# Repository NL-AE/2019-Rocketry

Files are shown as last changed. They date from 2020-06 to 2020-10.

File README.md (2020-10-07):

# 2019 Rocketry

Rocket for entry into the 2019 UKRoC challenge with 5 other friends.

Launch day: we put 4 motors instead of 3 and the rocket flew some 380m (about 120m over target). We lost the bottom stage so we now have half a rocket. 

In retrospective, painting it camouflage green was also not a good idea considering it landed in a green field.
Also I made the arduino write to the "DATALOG.TXT" instead of the file in the SD card called "data.txt" so we didnt get any data.

The control system looked like it worked since the rocket didnt have a rapid unplanned disassembly and shot straight upwards.

Before Launch
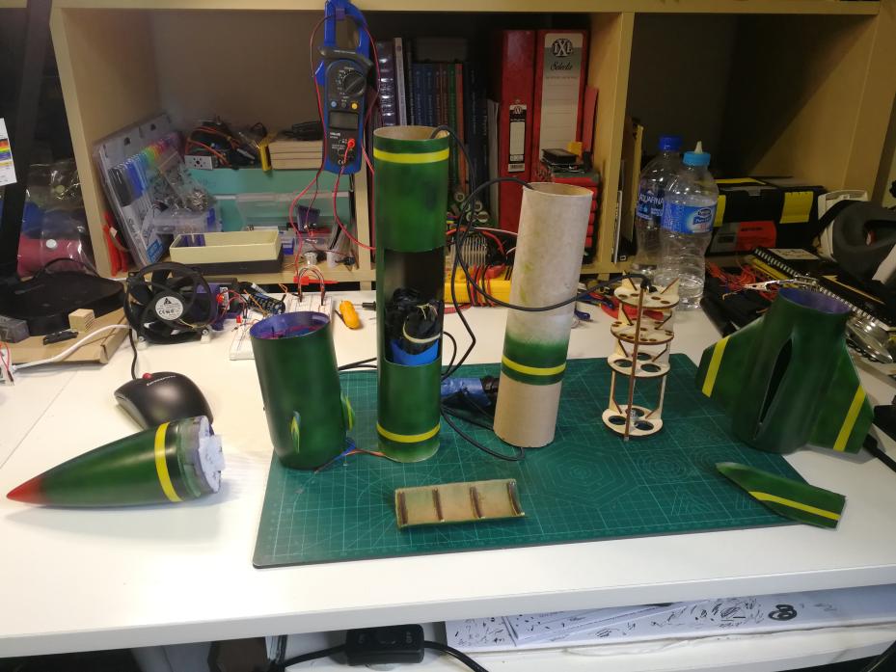
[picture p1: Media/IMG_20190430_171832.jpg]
Rocket in pieces


Ready for launch
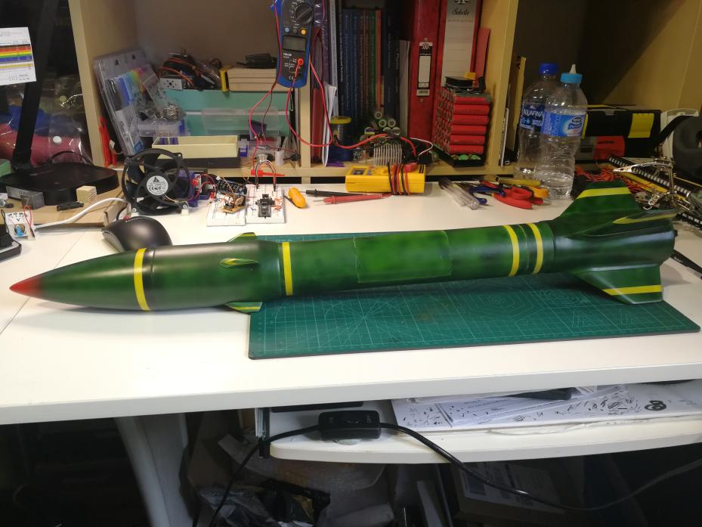
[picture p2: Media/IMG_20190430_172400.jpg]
Rocket togeter


The pile of electronics that controls it
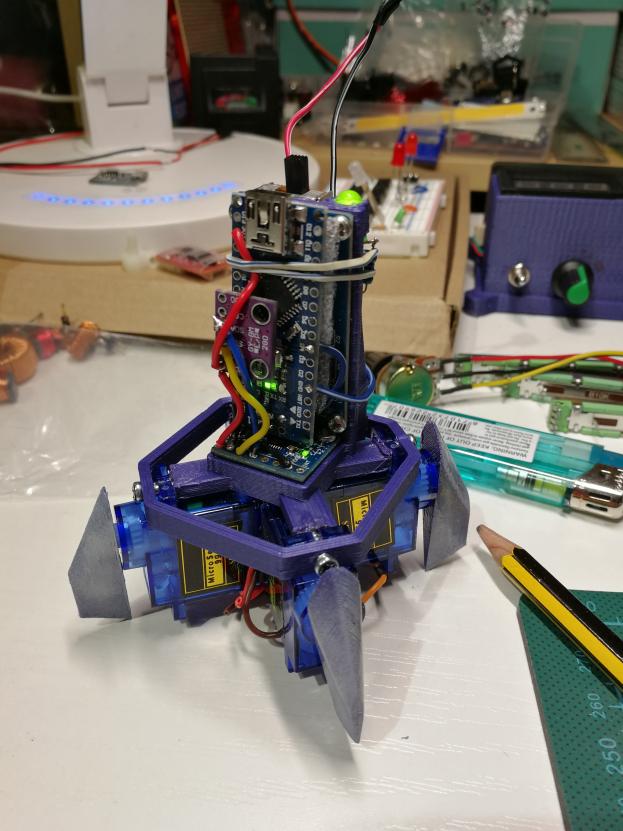
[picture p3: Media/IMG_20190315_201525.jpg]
Arduino pile


The launchpad that plugs into a camera tripod
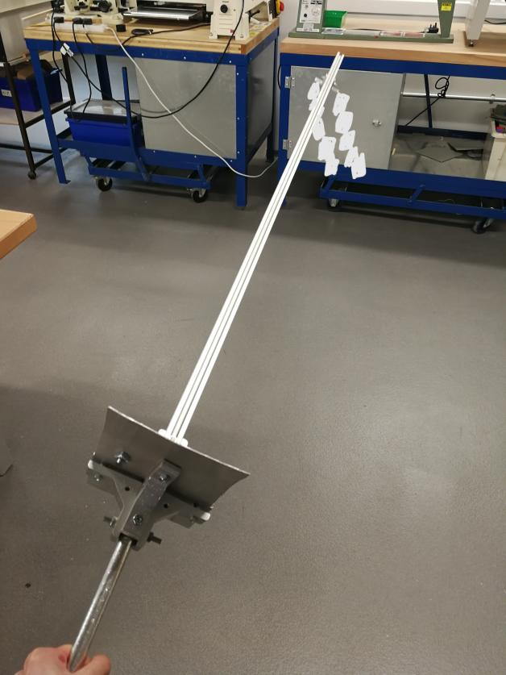
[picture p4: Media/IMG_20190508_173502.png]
Launchpad


Big red launch button that we didnt end up using
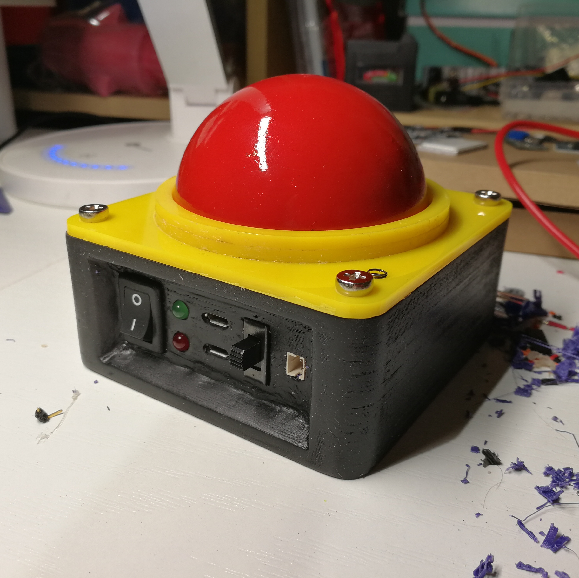
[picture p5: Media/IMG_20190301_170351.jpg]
button


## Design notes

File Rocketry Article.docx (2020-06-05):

Is it possible to create a self-stabilizing rocket?

Well yes of course, nowadays almost all missiles have a guidance system that allows for trajectories to be calculated and finely controlled. Despite the widespread use of this technology, it is mainly restricted to large corporations with huge RnD departments however, the rise of consumer electronics recently had given the ability for individuals to create complex circuitry and controllers. This will be the focus of this endeavour, is it possible to create a self-stabilizing model scale rocket?

The Control System

The brainbox of this operation will be the Arduino, a small programmable micro-controller (essentially a very small computer) which will read the pitch, yaw and roll as well as the altitude of the rocket and use that to control the angle of four fins mounted to the top of the rocket.

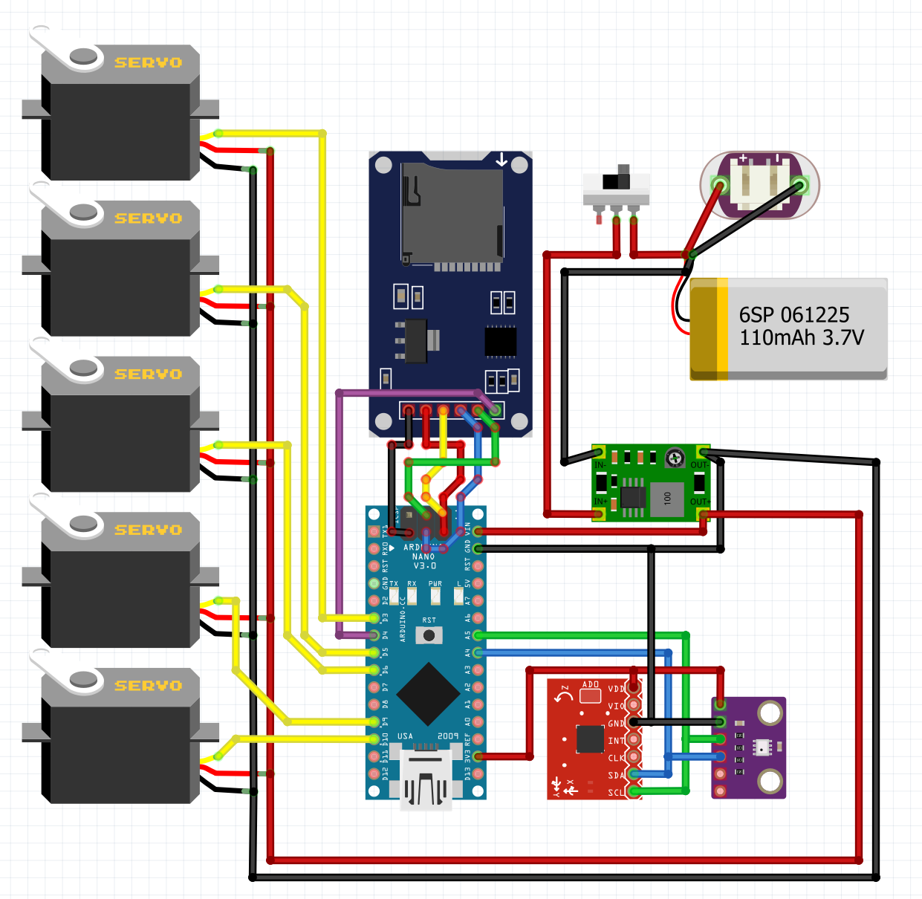
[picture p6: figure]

Secondary aims include to calculate the altitude of the rocket from atmospheric pressure readouts and to hopefully extrapolate velocity from it. Another aim is to use a SD card to record the data from the rocket and be able to act as a datalogger for analysis after launches.

Boost converter

Li-po battery

Power switch

Charging port

Gyroscope

Altimeter

SD card reader

Arduino

Circuit Diagram

Data input and outputs

Firstly, powering the components:

1) The voltage from the lithium polymer (li-po) battery is boosted from 3.7v (nominal cell voltage) to 6.0v since the other electronics run on 5v logic. The additional 1v is needed since there will be a small 0.7v voltage drop from the power regulator on the Arduino.
2) The Arduino then powers the gyroscope and altimeter at 3.3v since they run on 3.3v logic and will most likely become damaged when powered at 5v.
3) The servos are connected directly to the boost converter’s 6v as it means that no current needs to run through the Arduino to get to the servos. This is important as the servos will be drawing about 100mA under no load, and up to 500mA at full which the Arduino cannot supply without burning up.

Secondly, the controls:

1) The Arduino communicates with the modules and reads the angles off the gyroscope and the pressure off the altimeter, receiving data in the format of:

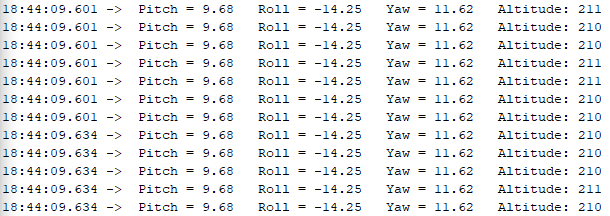
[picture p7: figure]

2) Since the altimeter outputs pressure in pascals, it needs to be converted into a altitude above sea level in Altitude(m)=13504.985×(1-((Pressure_(Pa))/101325)^0.190289 )

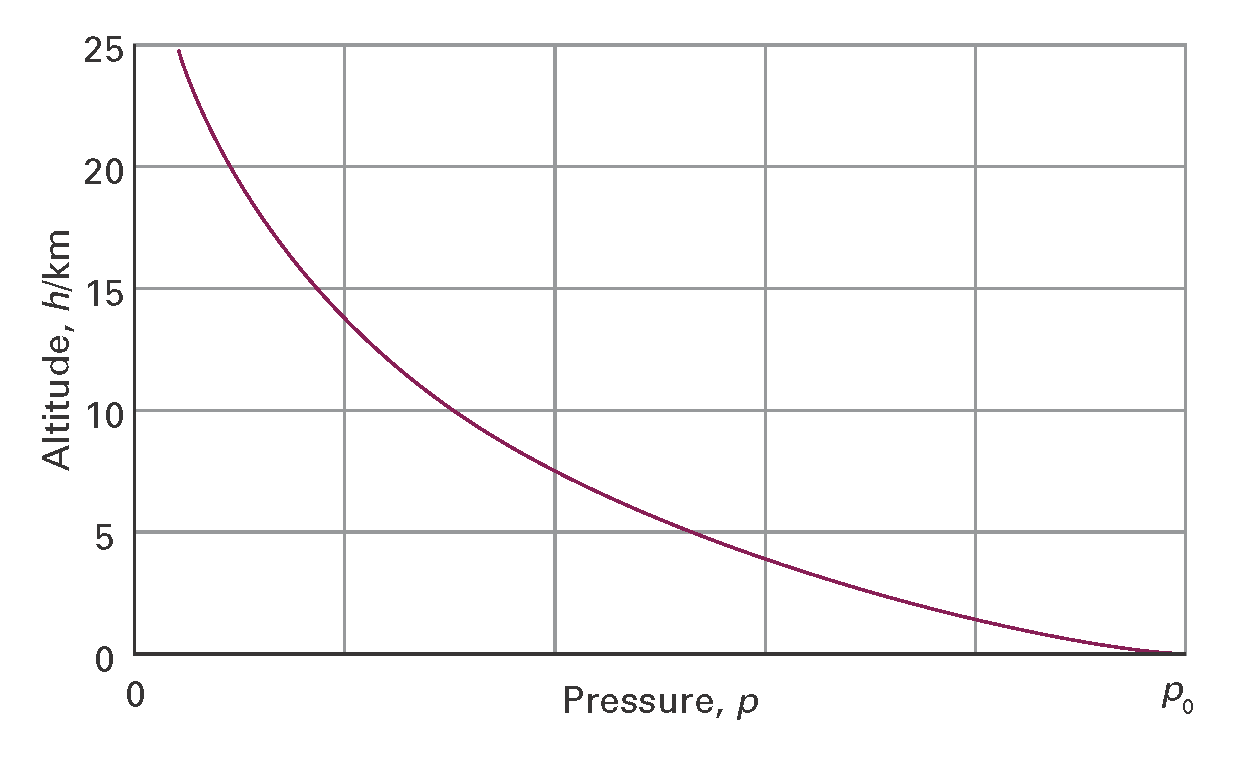
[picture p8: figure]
Image result for pressure to altitude formula

3) From the angles received, the Arduino will then send a signal to the servos along the yellow wires, instructing them to move to a different angle if necessary.

At this point, emerges the main problem of control, how much should the servos change angle?

PID controllers

If the angle change is too much, it will cause the rocket to over-correct, leading to the servos swinging back to correct the over-correction. This leads to a system that rapidly loses stability essentially balancing on a knife’s edge. What is needed is a system that actively measures the change in angle and corrects for it. Systems like this are called PID controllers and are used in inherently unstable scenarios such as self-balancing robots, temperature regulators or in this case, a model rocket.

PID controllers work by taking the difference in desired angle and current angle(called the “error”) and computing a needed angle change (called the “solution”) which is sent the servos to achieve that while monitoring the error constantly.

The 3 components of a PID controller are:

1) Proportional –

The controller takes the error and sets the solution to be proportional to that difference. If this is set too high, it will cause the problem as mentioned above and cause rapidly growing oscillations but set too low there will be little change in the error. Thus, something is needed to dampen the oscillations.

2) Derivative –

This considers the magnitude of the solution computed by the proportional and decreases it according to how small the error is. It is effectively a damper to the proportional part of the controller and stops the oscillations by lowering the solution according to how small the error it. However, another problem arises, if this is set too high, it will dampen the solution too much that the error will never be 0 (the system will never reach its desired value) as the dampening effect will become greater than the solution, leading to an equilibrium achieved just below the desired value. Thus, the last part of the PID controller is needed.

3) Integral –

This finds the integral between the current angle and the desired angle. The smaller the error, the larger this component becomes. It essentially pushes the solution just enough that the solution will become zero when the error is zero, thus achieving the desired angle.

Component | Too high | Too low
Proportional | Rapid oscillations | Changes very slowly
Derivative | Equilibrium achieved below desired angle | Rapid oscillations
Integral | Small, rapid oscillations | Never reaches desired angle

The main problem with controllers like this is that it requires extensive testing and tuning the constants for each of the components. Additionally, they constants would most likely need to change according to the relative wind speed, creating further problems.

Coupled with the need for complex calculations on the Arduino’s part just to compute the solution, as well as the resulting decreased refresh rate of this systems means that it is not very suitable for small scale rockets. It is possible to get around this hardware problem by using better micro-controllers however the prices for a control board rises very rapidly.

The Alternate Solution

The method of stabilization used in the end is a relatively simple system which has many advantages over a PID system. The process is:

1) Determining the angles of pitch, yaw and roll of the rocket.
2) Moving the servo motors so that they always are perpendicular to the ground, resulting in almost no further calculation needed as well as negating the opportunity for over-correcting to occur.

Working in 2 dimensions, if the rocket is angled slightly to the left, the fins pitch to the right (relative to the rocket) but remain perpendicular to the ground. This results in the rocket experiencing a force which pushes it to zero degrees or vertical.

In the end, we opted for this solution since it make the code a lot easier as well as being less demanding on the Arduino. This also meant that we did not need to perform any wind tunnel experiments to adjust the controller, also a highly time-consuming task. As stated above, the settings would most likely need to change according to wind speed and with the rocket reaching up to 70ms⁻¹, it would be impossible to simulate this in the wind tunnel setup we had.

Results

Following the launch on the 4th May, we saw that the correction system functioned perfectly with the rocket flying straight up, overshooting the desired height as it was our first launch. Unfortunately, due to the rocket reaching a high altitude of 371m, the rocket drifted on the parachutes for a very long distance away from the launch site, resulting in the bottom part of the rocket being lost, preventing us from performing further launches. Despite top half of the rocket containing the electronics being recovered, we collected no data due to either a programming error or other hardware errors.

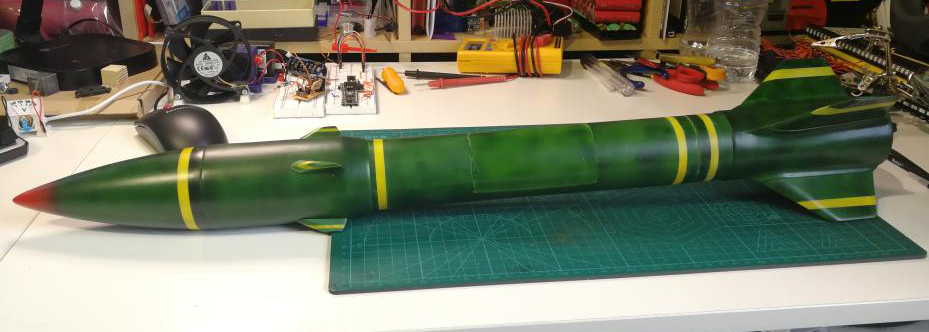
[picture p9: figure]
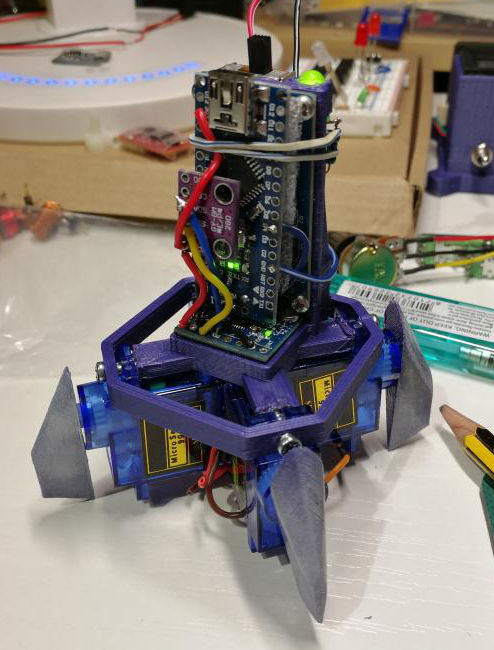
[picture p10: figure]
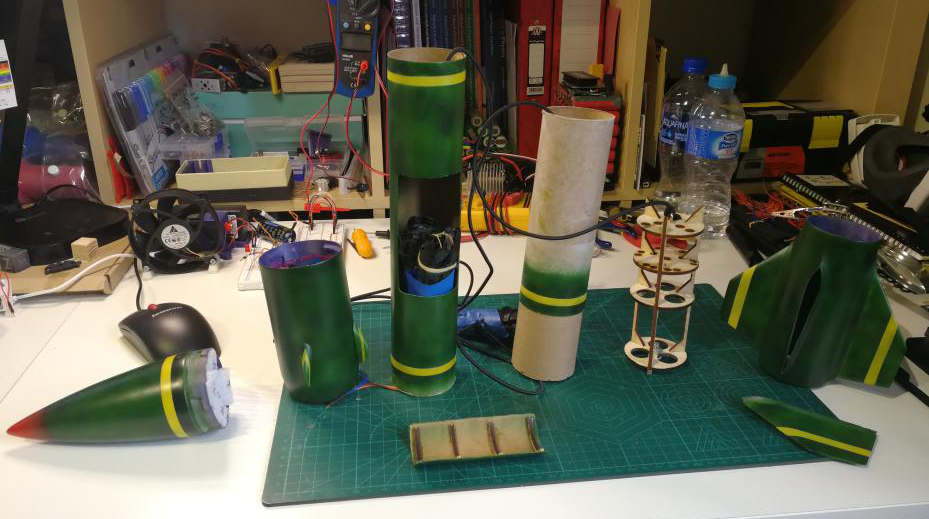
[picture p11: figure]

Left to right:

Nosecone, electronics bay, middle tube section, bottom stage, motor mounts, fin support structure.

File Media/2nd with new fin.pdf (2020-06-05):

## Rocket Design

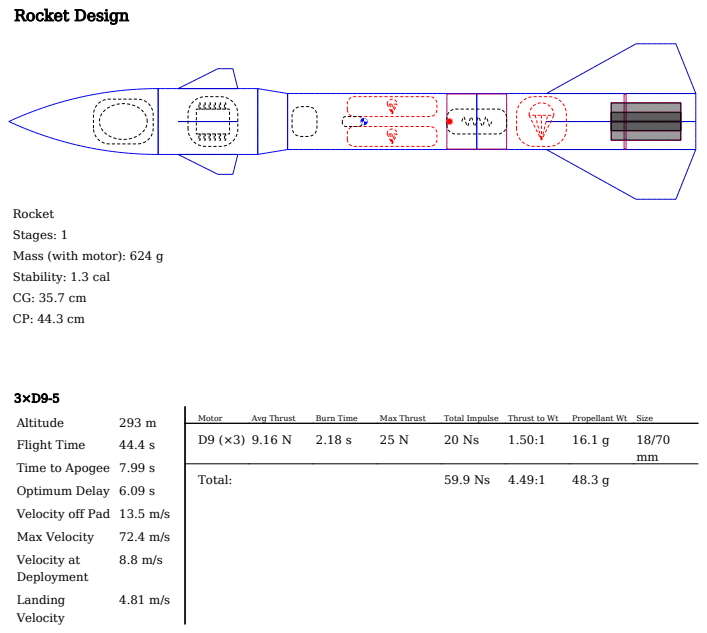
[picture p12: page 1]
Altitude; Flight Time; Optimum Delay 6.09 s; Max Velocity; Velocity at; Deployment; Landing; Velocity; Motor; Avg Thrust; Burn Time; Max Thrust; Total Impulse; Thrust to Wt; Propellant Wt Size; Total:

Rocket
Stages: 1
Mass (with motor): 624 g
Stability: 1.3 cal

Time to Apogee 7.99 s

Velocity off Pad 13.5 m/s

## Parts Detail

Sustainer

Nose cone | 3D Print

(1.23 g/cm³)

Ogive | Len: 15 cm | Mass: 20.7 g
Body tube | 3D Print

(1.23 g/cm³)

Diain 6.46 cm
Diaout 6.62 cm
Len: 10 cm | Mass: 20.2 g
Egg | Diaout 4.5 cm | Mass: 63 g
Arduino Fins (4) | 3D Print

(1.23 g/cm³)

Thick: 0.5 cm | Mass: 3 g
Arduino + Payloads | Diaout 5 cm | Mass: 73 g
Transition | 3D Print

(1.23 g/cm³)

Fore Dia: 6.62
cm
Aft Dia: 5.63
cm
Len: 3 cm | Mass: 8.46 g
Main Body | Cardboard

(0.68 g/cm³)

Diain 5.53 cm
Diaout 5.63 cm
| Len: 19 cm | Mass: 11.3 g
Parachute 1 | Ripstop nylon

(67 g/m²)

Diaout 50 cm | Len: 9 cm | Mass: 16.4 g
Shroud Lines | Elastic cord
(round 2 mm,
1/16 in)

(1.8 g/m)

Lines: 6 | Len: 30 cm
Parachute 1 | Ripstop nylon

(67 g/m²)

Diaout 50 cm | Len: 9 cm | Mass: 16.4 g
Shroud Lines | Elastic cord
(round 2 mm,
1/16 in)

(1.8 g/m)

Lines: 6 | Len: 30 cm
Parachute Servo | Diaout 1 cm | Mass: 10 g
Unspecified | Diaout 3 cm | Mass: 200 g
Boost | Cardboard

(0.68 g/cm³)

Diain | 5.54 cm
| Diaout 5.63 cm
Len: 22 cm | Mass: 11.8 g
Back Fins (4) | Balsa

(0.17 g/cm³)

| Thick: 1 cm | Mass: 27.5 g
Engines | Cardboard

(0.68 g/cm³)

Diain | 1.8 cm
| Diaout 1.9 cm
Len: 7 cm | Mass: 4.15 g
Tube Coupler | Cardboard

(0.68 g/cm³)

Diain | 5.34 cm
| Diaout 5.54 cm
Len: 6 cm | Mass: 6.97 g
Shock cord | Elastic cord
(round 2 mm,
1/16 in)

(1.8 g/m)

Len: 40 cm | Mass: 0.72 g
Parachute Back | Ripstop nylon

(67 g/m²)

Diaout 45 cm | Len: 5 cm | Mass: 13.9 g
Shroud Lines | Elastic cord
(round 2 mm,
1/16 in)

(1.8 g/m)

Lines: 6 | Len: 30 cm
Bulkhead | Cardboard

(0.68 g/cm³)

Diaout 5.54 cm Len: 0.2 cm Mass: 27 g

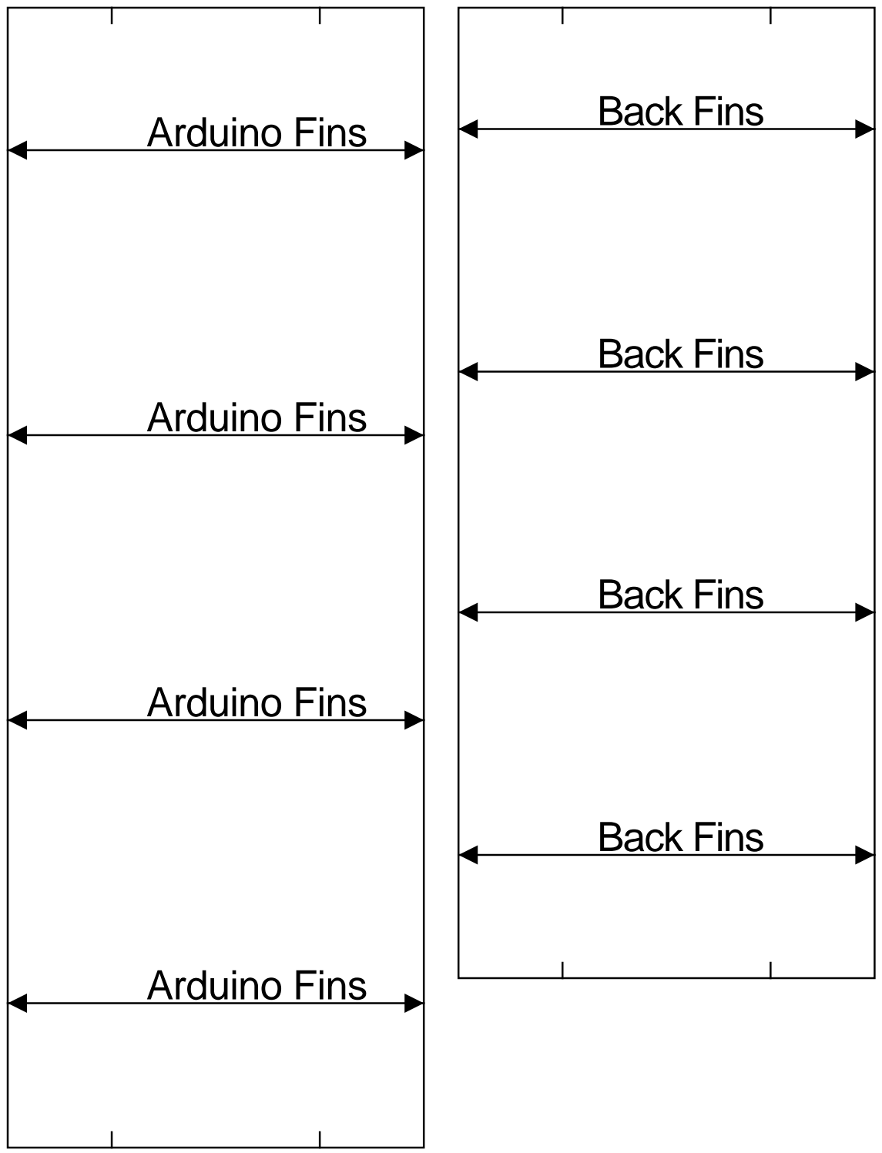
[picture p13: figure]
Arduino Fins; Back Fins

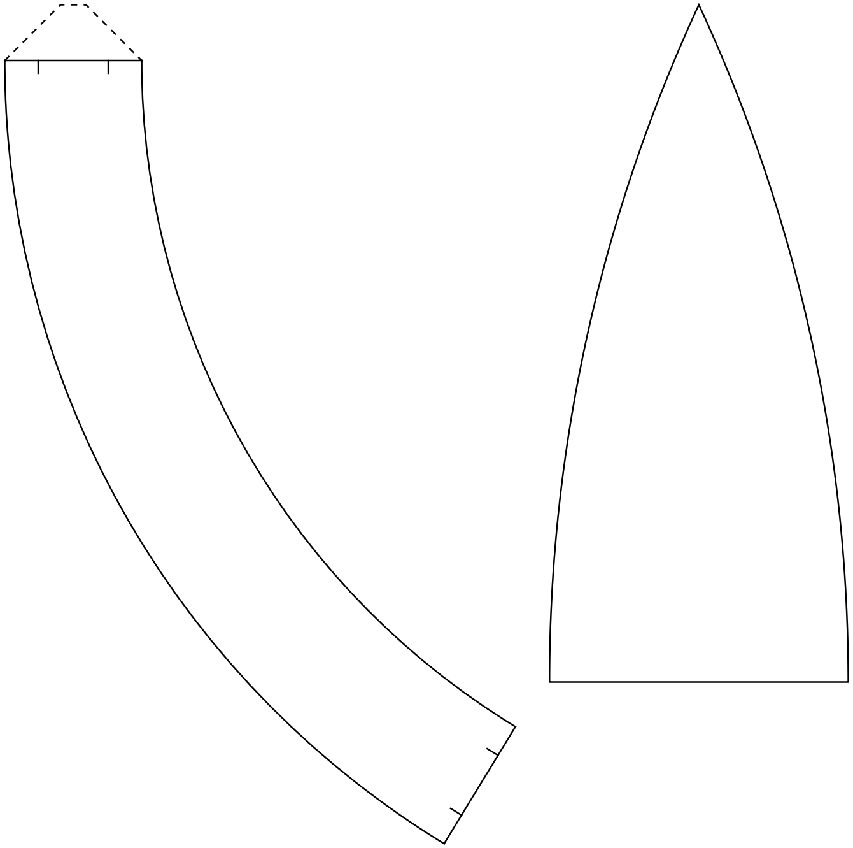
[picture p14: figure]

# in cm

cm
in

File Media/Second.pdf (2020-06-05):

## Rocket Design

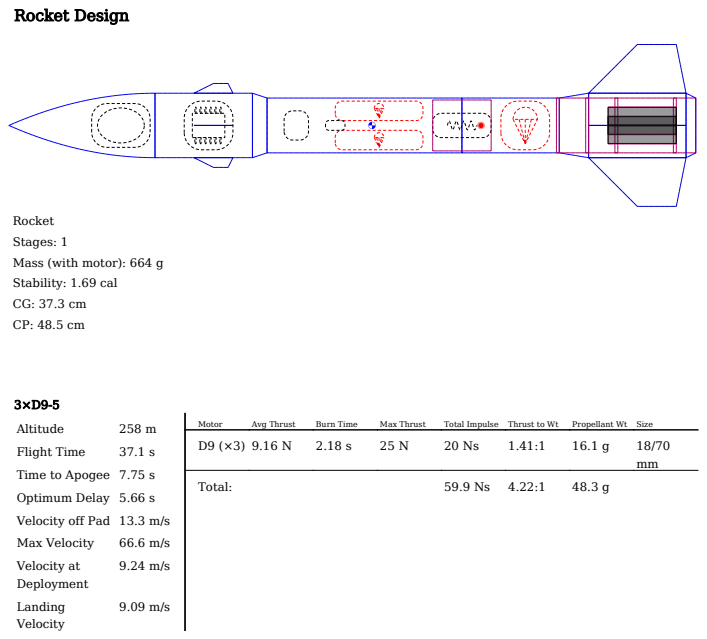
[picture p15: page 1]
Altitude; Flight Time; Optimum Delay 5.66 s; Max Velocity; Velocity at; Deployment; Landing; Velocity; Motor; Avg Thrust; Burn Time; Max Thrust; Total Impulse; Thrust to Wt; Propellant Wt Size; Total:

Rocket
Stages: 1
Mass (with motor): 664 g
Stability: 1.69 cal

Time to Apogee 7.75 s

Velocity off Pad 13.3 m/s

## Parts Detail

Sustainer

Nose cone | 3D Print

(1.23 g/cm³)

Parabolic
series
Len: 15 cm | Mass: 21 g
Body tube | 3D Print

(1.23 g/cm³)

Diain 6.46 cm
Diaout 6.62 cm
Len: 10 cm | Mass: 20.2 g
Egg | Diaout 4.5 cm | Mass: 63 g
Arduino Fins (4) | Balsa

(0.17 g/cm³)

| Thick: 1 cm | Mass: 4 g
Arduino + Payloads | Diaout 5 cm | Mass: 73 g
Transition | 3D Print

(1.23 g/cm³)

| Fore Dia: 6.62 cm Aft Dia: 5.63 cm
Len: 1.5 cm | Mass: 4.39 g
Main Body | Cardboard

(0.68 g/cm³)

Diain 5.53 cm
Diaout 5.63 cm
| Len: 20 cm | Mass: 11.9 g
Parachute 1 | Ripstop nylon

(67 g/m²)

Diaout 50 cm | Len: 9 cm | Mass: 16.4 g
Shroud Lines | Elastic cord
(round 2 mm,
1/16 in)

(1.8 g/m)

Lines: 6 | Len: 30 cm
Parachute 1 | Ripstop nylon

(67 g/m²)

Diaout 50 cm | Len: 9 cm | Mass: 16.4 g
Shroud Lines | Elastic cord
(round 2 mm,
1/16 in)

(1.8 g/m)

Lines: 6 | Len: 30 cm
Parachute Servo | Diaout 1 cm | Mass: 10 g
Unspecified | Diaout 3 cm | Mass: 200 g
Body tube | Cardboard

(0.68 g/cm³)

Diain | 5.23 cm
| Diaout 5.63 cm
Len: 10 cm | Mass: 23.2 g
Shock cord | Elastic cord
(round 2 mm,
1/16 in)

(1.8 g/m)

Len: 40 cm | Mass: 0.72 g
Parachute Back | Ripstop nylon

(67 g/m²)

Diaout 45 cm | Len: 5 cm | Mass: 13.9 g
Shroud Lines | Elastic cord
(round 2 mm,
1/16 in)

(1.8 g/m)

Lines: 6 | Len: 30 cm
Tube Coupler | Cardboard

(0.68 g/cm³)

Diain 5.03 cm
Diaout 5.23 cm
Len: 6 cm | Mass: 6.58 g
Transition | Cardboard

(0.68 g/cm³)

Fore Dia: 5.63
cm
Aft Dia: 6.63
cm
Len: 3 cm | Mass: 0 g
Boost | Cardboard

(0.68 g/cm³)

Diain 6.54 cm
Diaout 6.63 cm

Len: 10 cm Mass: 6.33 g

Back Fins (4) | Balsa

(0.17 g/cm³)

Thick: 1 cm | Mass: 20 g
Engines | Cardboard

(0.68 g/cm³)

Diain 1.8 cm
Diaout 1.9 cm
Len: 7 cm | Mass: 4.15 g
Inner Tube | Cardboard

(0.68 g/cm³)

Diain 5.53 cm
Diaout 5.63 cm
Len: 14 cm | Mass: 32.4 g
Bulkhead | Cardboard

(0.68 g/cm³)

Diaout 5.63 cm Len: 0.3 cm | Mass: 0 g
Bulkhead | Cardboard

(0.68 g/cm³)

Diaout 5.63 cm Len: 0.3 cm | Mass: 0 g
Bulkhead | Cardboard

(0.68 g/cm³)

Diaout 5.63 cm Len: 0.3 cm | Mass: 27 g
Bulkhead | Cardboard

(0.68 g/cm³)

Diaout 5.63 cm Len: 0.3 cm | Mass: 0 g
Transition | Cardboard

(0.68 g/cm³)

Fore Dia: 6.63
cm
Aft Dia: 5.63
cm
Len: 1 cm | Mass: 0 g

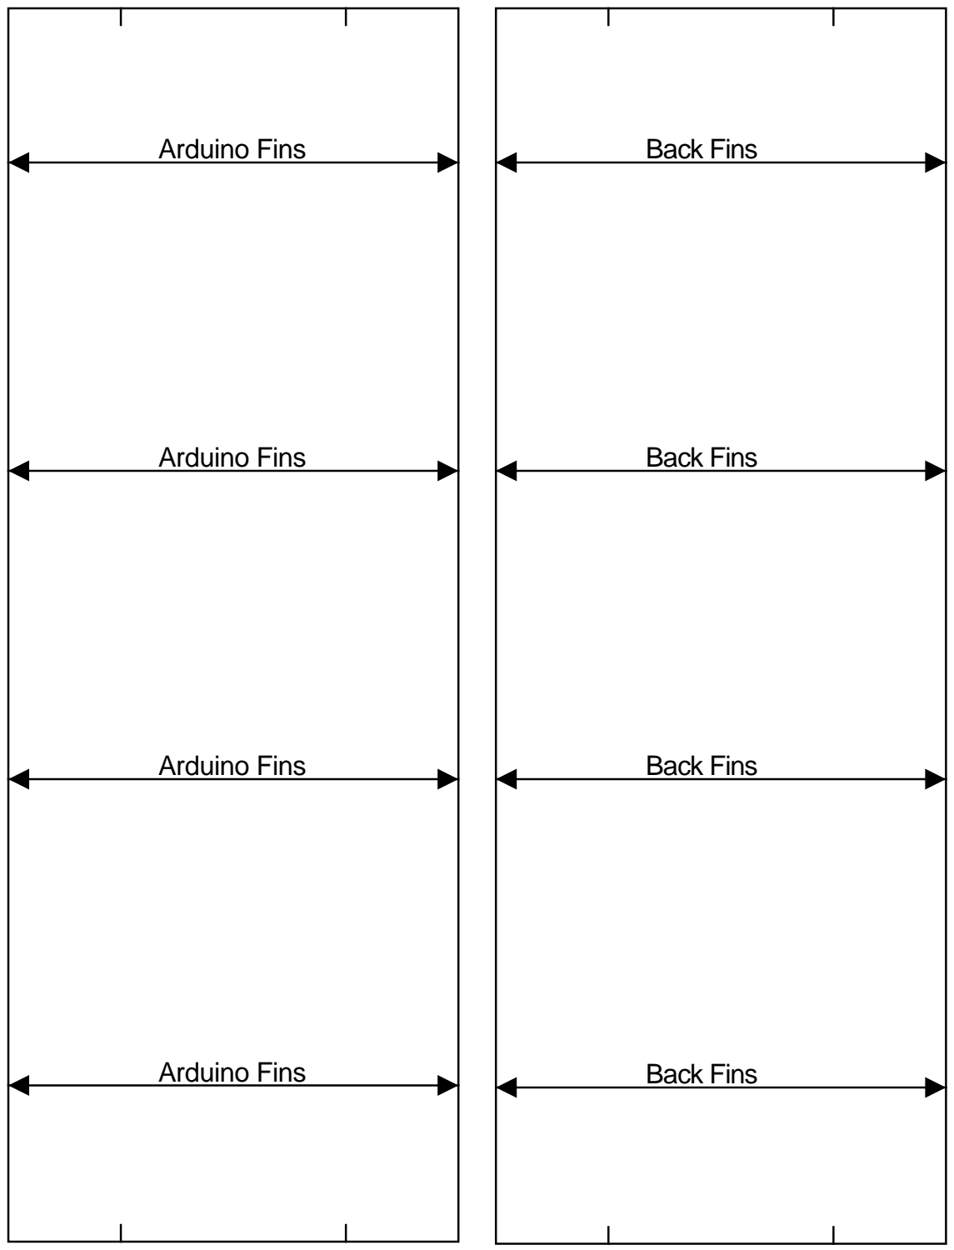
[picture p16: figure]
Arduino Fins; Back Fins

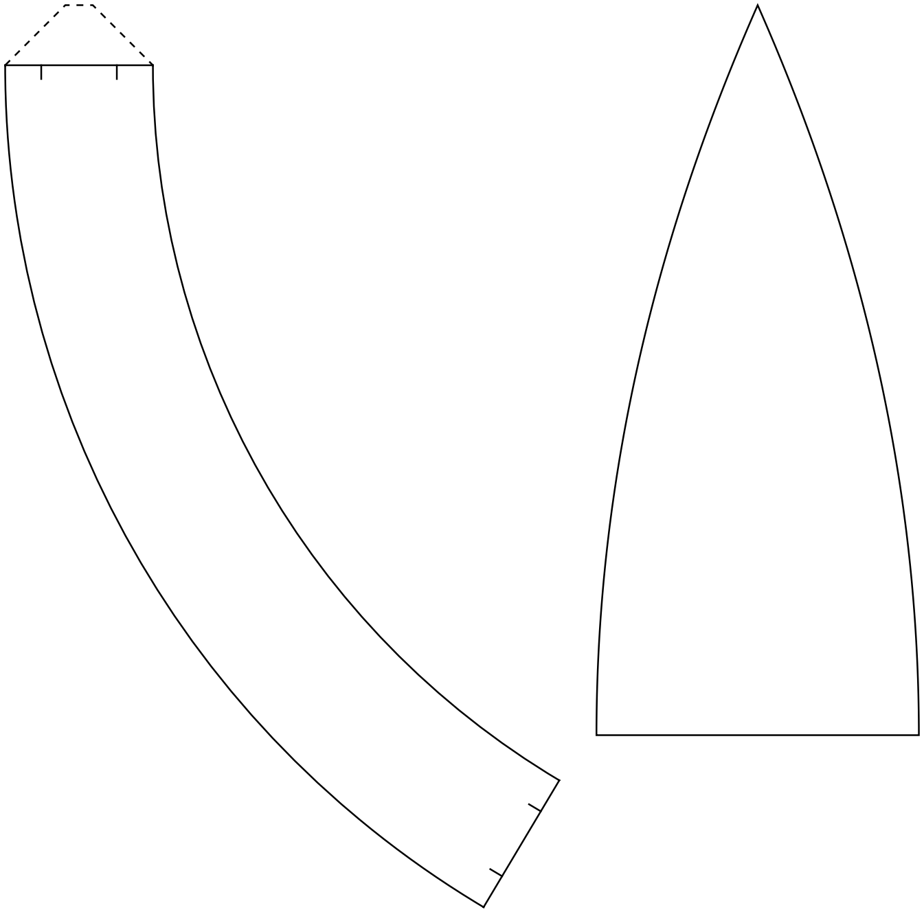
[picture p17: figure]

## in cm

cm
in

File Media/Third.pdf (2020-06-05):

## Rocket Design

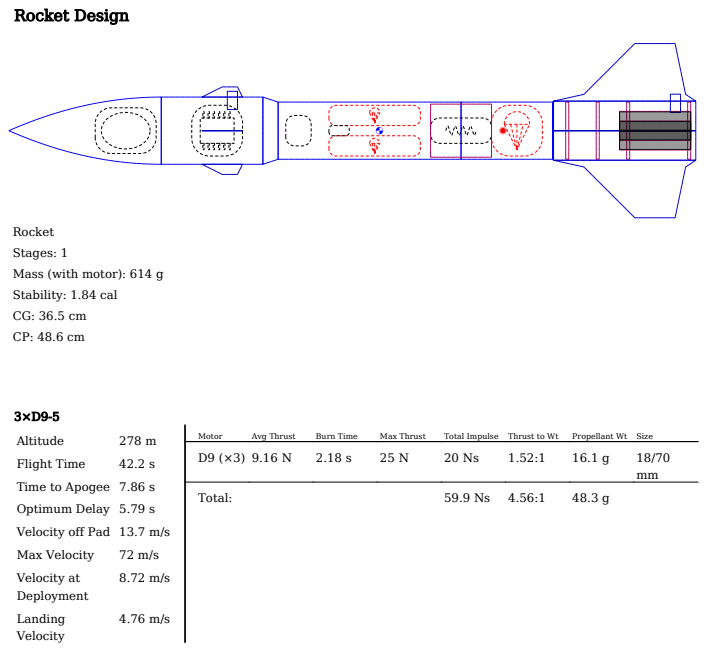
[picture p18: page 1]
Altitude; Flight Time; Optimum Delay 5.79 s; Max Velocity; Velocity at; Deployment; Landing; Velocity; Motor; Avg Thrust; Burn Time; Max Thrust; Total Impulse; Thrust to Wt; Propellant Wt Size; Total:

Rocket
Stages: 1
Mass (with motor): 614 g
Stability: 1.84 cal

Time to Apogee 7.86 s

Velocity off Pad 13.7 m/s

## Parts Detail

Sustainer

Nose cone | 3D Print

(1.23 g/cm³)

Parabolic
series
Len: 15 cm | Mass: 21 g
Body tube | 3D Print

(1.23 g/cm³)

Diain 6.46 cm
Diaout 6.62 cm
Len: 10 cm | Mass: 20.2 g
Egg | Diaout 4.5 cm | Mass: 63 g
Arduino Fins (4) | Balsa

(0.17 g/cm³)

| Thick: 1 cm | Mass: 4 g
Arduino + Payloads | Diaout 5 cm | Mass: 79 g
Launch lug | Cardboard

(0.68 g/cm³)

Diain | 1.72 cm
| Diaout 1.8 cm
Len: 1 cm | Mass: 0.15 g
Transition | 3D Print

(1.23 g/cm³)

| Fore Dia: 6.62 cm Aft Dia: 5.63 cm
Len: 1.5 cm | Mass: 4.39 g
Main Body | Cardboard

(0.68 g/cm³)

Diain 5.53 cm
Diaout 5.63 cm
| Len: 18 cm | Mass: 10.7 g
Parachute 1 | Ripstop nylon

(67 g/m²)

Diaout 50 cm | Len: 9 cm | Mass: 16.4 g
Shroud Lines | Elastic cord
(round 2 mm,
1/16 in)

(1.8 g/m)

Lines: 6 | Len: 30 cm
Parachute 1 | Ripstop nylon

(67 g/m²)

Diaout 50 cm | Len: 9 cm | Mass: 16.4 g
Shroud Lines | Elastic cord
(round 2 mm,
1/16 in)

(1.8 g/m)

Lines: 6 | Len: 30 cm
Parachute Servo | Diaout 1 cm | Mass: 10 g
Unspecified | Diaout 3 cm | Mass: 150 g
Body tube | Cardboard

(0.68 g/cm³)

Diain | 5.23 cm
| Diaout 5.63 cm
Len: 9 cm | Mass: 20.9 g
Shock cord | Elastic cord
(round 2 mm,
1/16 in)

(1.8 g/m)

Len: 40 cm | Mass: 0.72 g
Parachute Back | Ripstop nylon

(67 g/m²)

Diaout 45 cm | Len: 5 cm | Mass: 13.9 g
Shroud Lines | Elastic cord
(round 2 mm,
1/16 in)

(1.8 g/m)

Lines: 6 | Len: 30 cm
Tube Coupler | Cardboard

(0.68 g/cm³)

Diain 5.03 cm
Diaout 5.23 cm
Len: 6 cm | Mass: 6.58 g
Transition | Cardboard

(0.68 g/cm³)

Fore Dia: 5.63
cm
Aft Dia: 5.82
cm

Len: 0.1 cm Mass: 0 g

Boost | Cardboard

(0.68 g/cm³)

Diain 5.73 cm
Diaout 5.82 cm
Len: 14 cm | Mass: 30 g
Engines | Cardboard

(0.68 g/cm³)

Diain 1.8 cm
Diaout 1.9 cm
Len: 7 cm | Mass: 4.15 g
Bulkhead | Cardboard

(0.68 g/cm³)

Diaout 5.63 cm Len: 0.3 cm | Mass: 0 g
Bulkhead | Cardboard

(0.68 g/cm³)

Diaout 5.63 cm Len: 0.3 cm | Mass: 0 g
Bulkhead | Cardboard

(0.68 g/cm³)

Diaout 5.63 cm Len: 0.3 cm | Mass: 27 g
Bulkhead | Cardboard

(0.68 g/cm³)

Diaout 5.63 cm Len: 0.3 cm | Mass: 0 g
Fin Fillet (4) | Cardboard

(0.68 g/cm³)

Thick: 1 cm | Mass: 26 g
Launch lug | Cardboard

(0.68 g/cm³)

Diain 1.72 cm
Diaout 1.8 cm
Len: 1 cm | Mass: 0.15 g

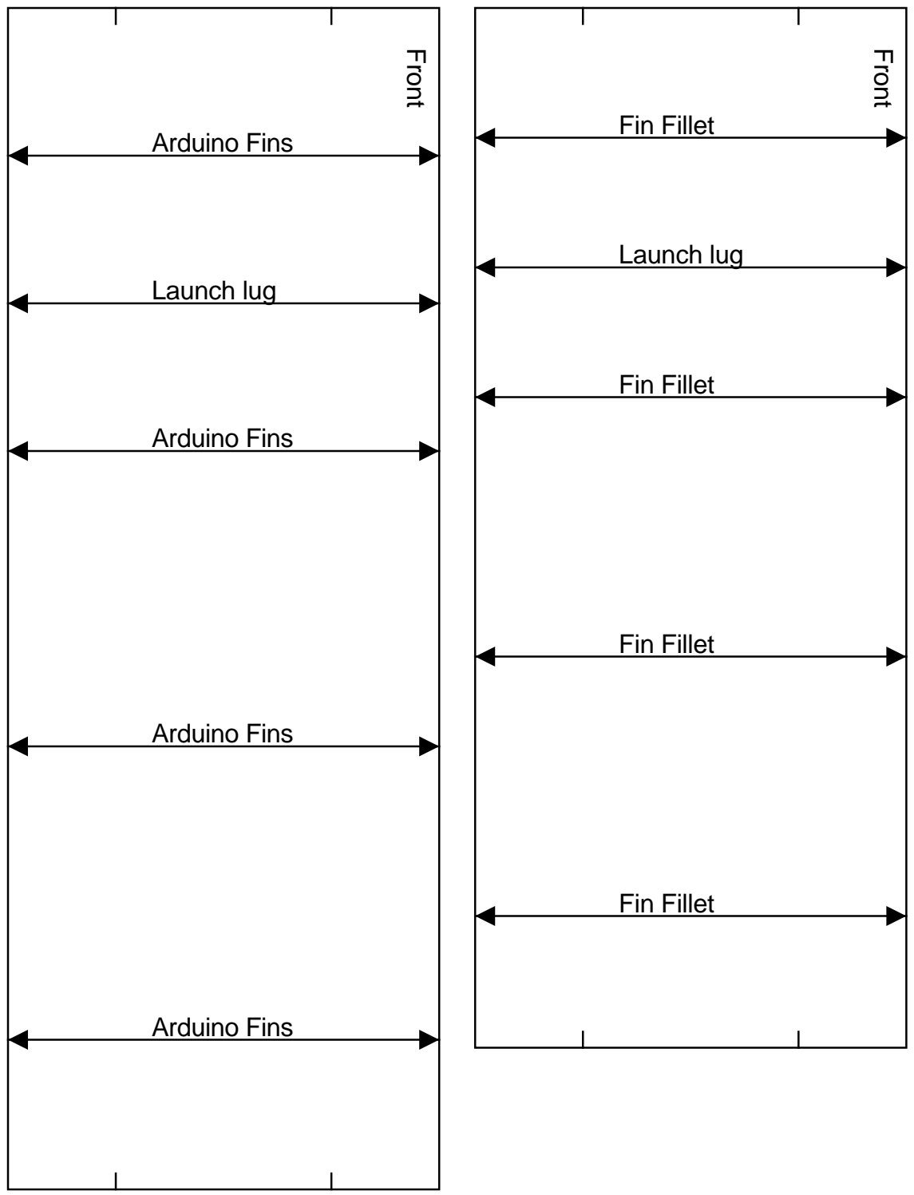
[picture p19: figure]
Arduino Fins; Launch lug; Front; Fin Fillet

## in cm

cm
in

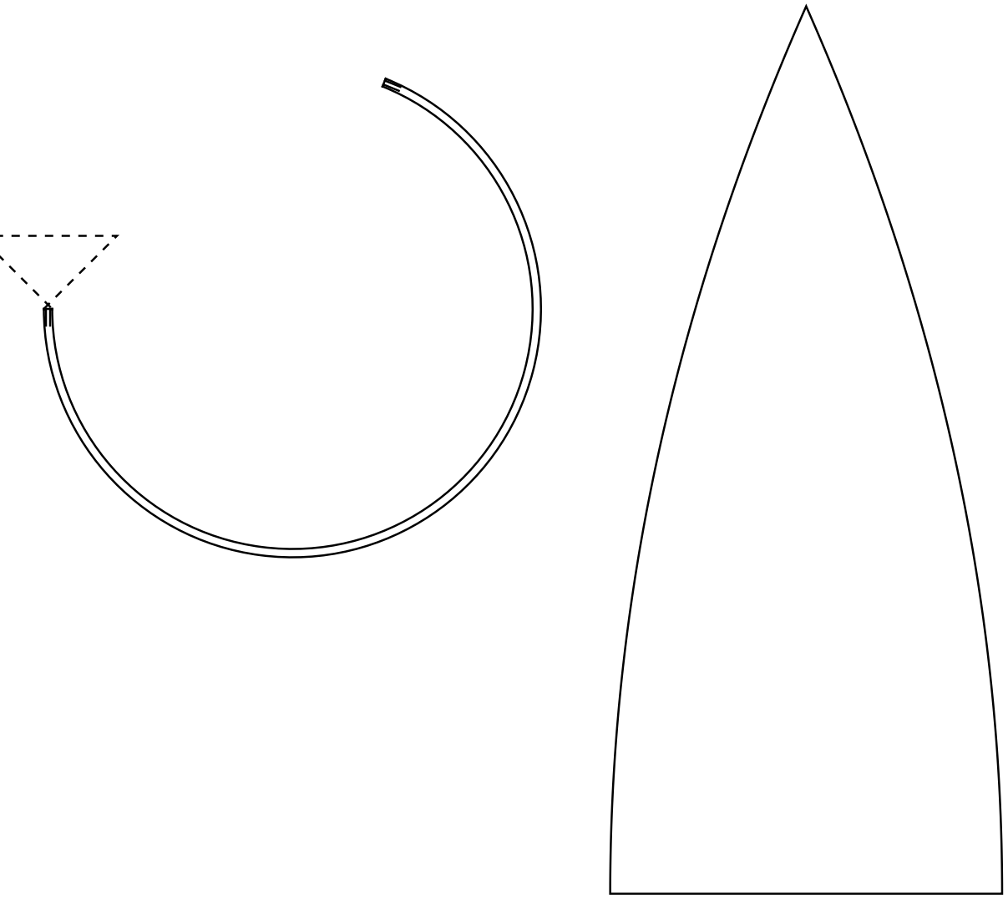
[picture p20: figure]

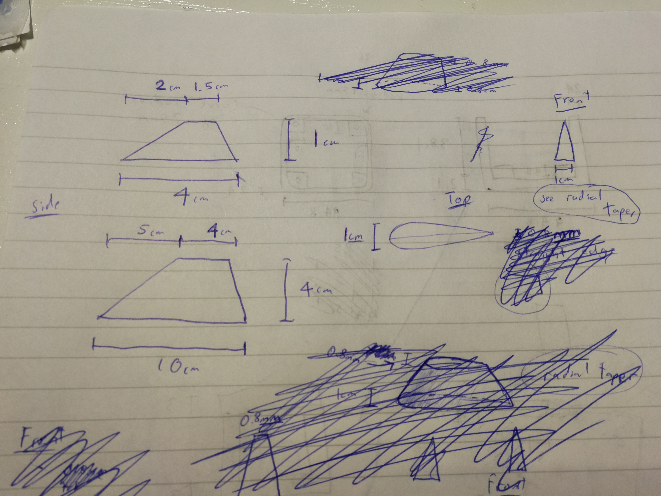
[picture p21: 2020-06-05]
Media/Fin Designs.jpg

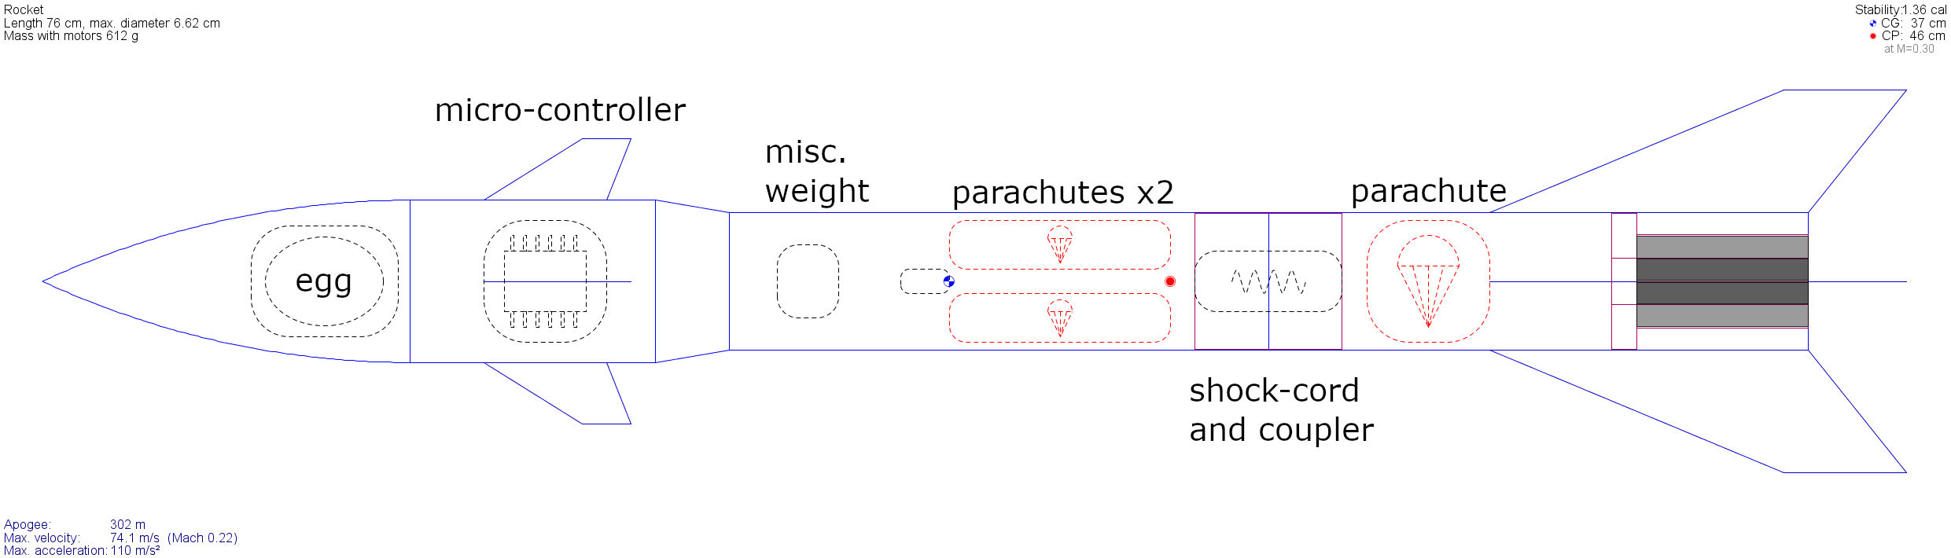
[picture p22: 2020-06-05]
Media/first.PNG

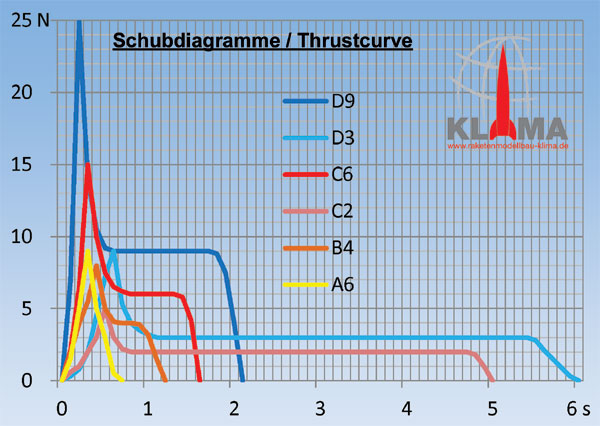
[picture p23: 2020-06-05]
Motor thrusts.jpg

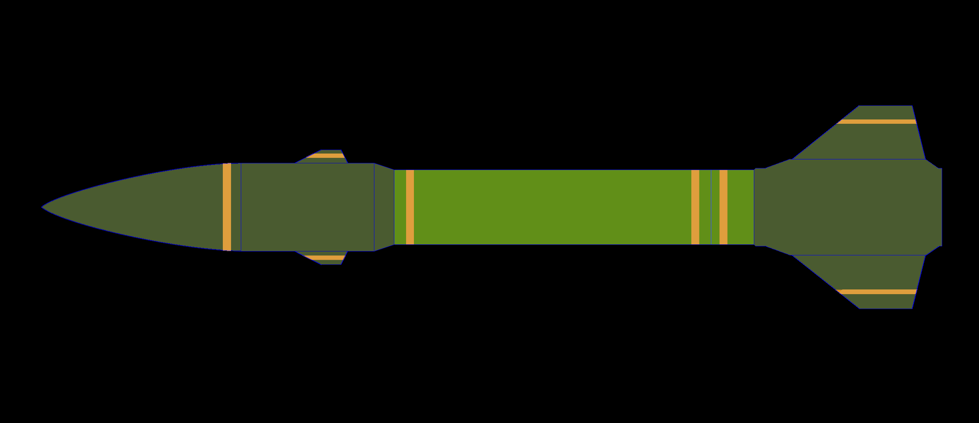
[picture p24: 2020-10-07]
Media/Paint Scheme.png

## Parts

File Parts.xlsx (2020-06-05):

Part Name | Option | Link | Quantity | Price/£ | Total Price
Motors | D9-5 | https://www.modelrockets.co.uk/shop/beginners-essentials/d9-six-pack-18mm-rocket-motor-p-3305.html | 6 | 22.99 | 137.94
Tubing |  | https://www.modelrockets.co.uk/shop/body-tubes/body-tube-bt-70-brukroc-2019-p-1172.html | 2 | 6.99 | 13.98
Nylon sheet | 2 meter | https://www.amazon.co.uk/Polyester-Resistant-Waterproof-Fabric-150cms/dp/B01H7EE02K | 2 | 3.75 | 7.50
Kevlar thread |  | https://www.amazon.co.uk/Black-Kevlar%C2%AE-Thread/dp/B00TLUMV3O | 1 | 5.99 | 5.99
Gyro |  | https://www.amazon.co.uk/COM-FOUR-MPU-6050-gyroscope-accelerometer-Arduino/dp/B00WE3XW7E | 1 | 6.99 | 6.99
Step up |  | https://www.amazon.co.uk/DaoRier-Voltage-Regulator-Adjustable-Converter/dp/B06WD5BBP8?s=electronics | 2 | 1.65 | 3.30
Altimeter |  | https://www.amazon.co.uk/MissBirdler-Pressure-Altimeter-Breaktout-Rasperry/dp/B01N51WHYP | 2 | 4.34 | 8.68
Battery |  | https://www.amazon.co.uk/400mAh-Battery-Walkera-Quadcopter-Charger/dp/B071ZDWSVG | 1 | 11.99 | 11.99
Servo |  | https://www.amazon.co.uk/High-Key-Helicopter-Airplane-Control/dp/B07FPPRMJS | 1 | 16.99 | 16.99
Arduino (nano) |  | https://www.amazon.co.uk/Cylewet-ATMEGA328P-Micro-controller-Arduino-CLW1060/dp/B06XT5LYJ4 | 1 | 8.99 | 8.99
SD Reader |  | https://www.amazon.co.uk/kwmobile-Reader-Adapter-Arduino-Microcontrollers/dp/B06XHJTGGC | 2 | 6.40 | 12.80
SD Card |  | https://www.amazon.co.uk/Verbatim-44081-Class-Micro-Adapter/dp/B00CBAUI40?s=electronics-accessories | 2 | 2.39 | 4.78
Firefly Alti |  | http://www.perfectflitedirect.com/firefly-altimeter/ | 1 | 17.60 | 17.60
 |  |  |  | Total | 257.53

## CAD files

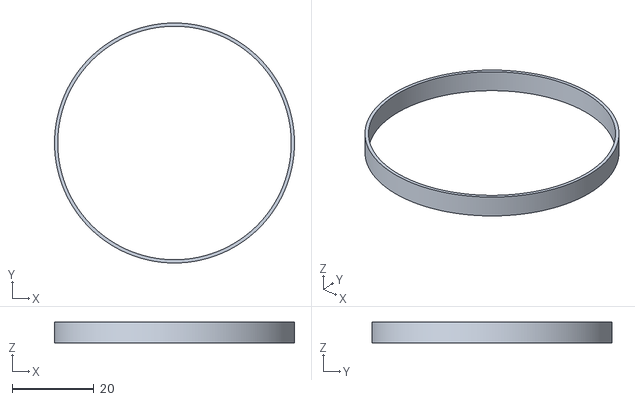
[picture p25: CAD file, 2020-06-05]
parts/Fin Slot Marker.stl
58.8 x 58.8 x 5.05

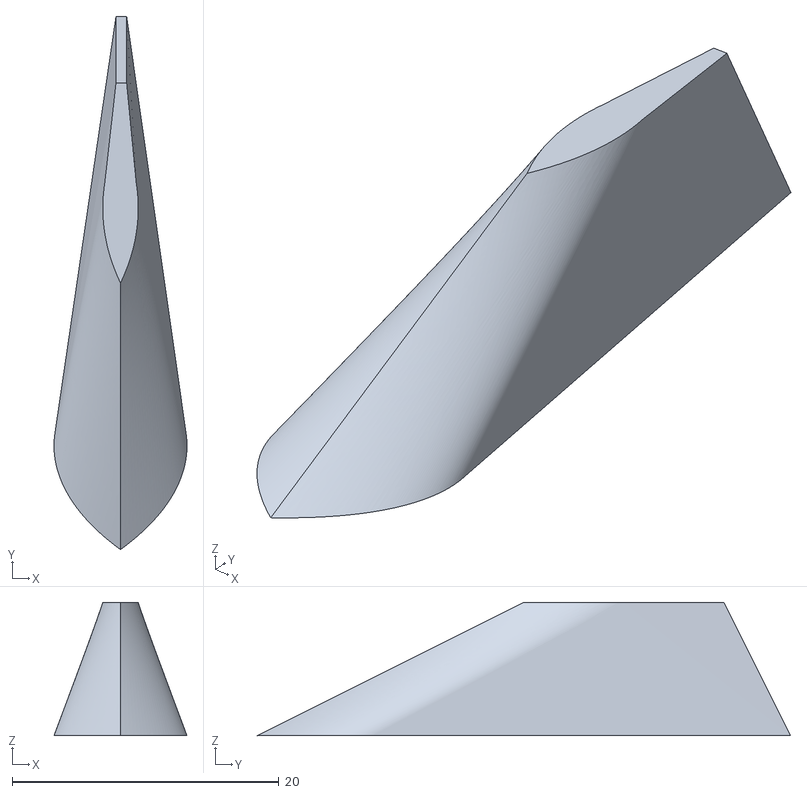
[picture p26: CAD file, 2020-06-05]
parts/fins/new - smol fin.stl
9.98 x 40.0 x 10.0

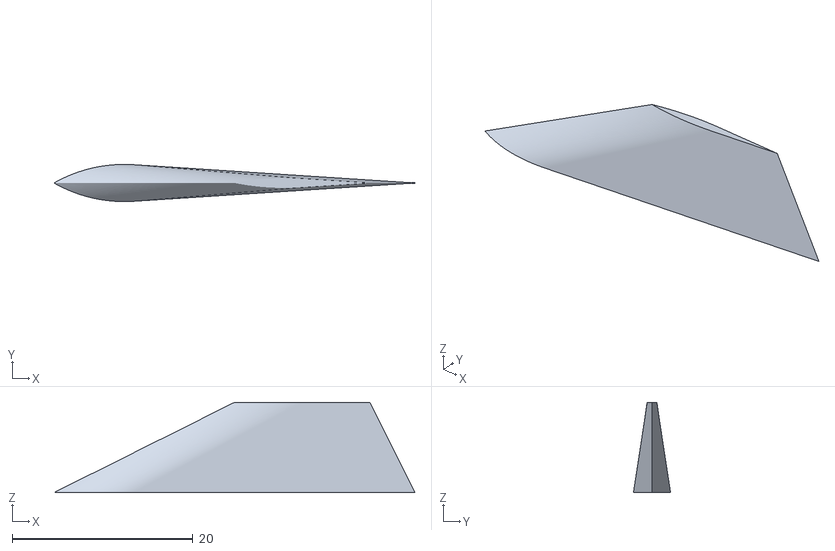
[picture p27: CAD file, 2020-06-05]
parts/fins/smol fin.stl
40.0 x 4.12 x 10.0

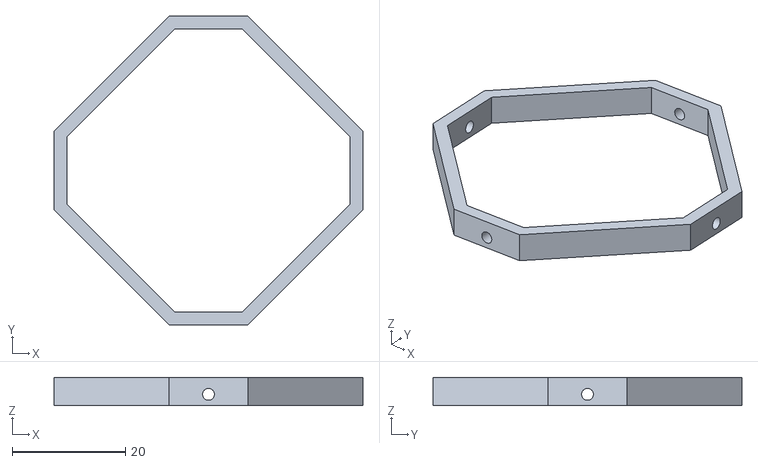
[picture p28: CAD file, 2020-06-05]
parts/Servo Stand bottom.stl
54.6 x 54.6 x 5.00

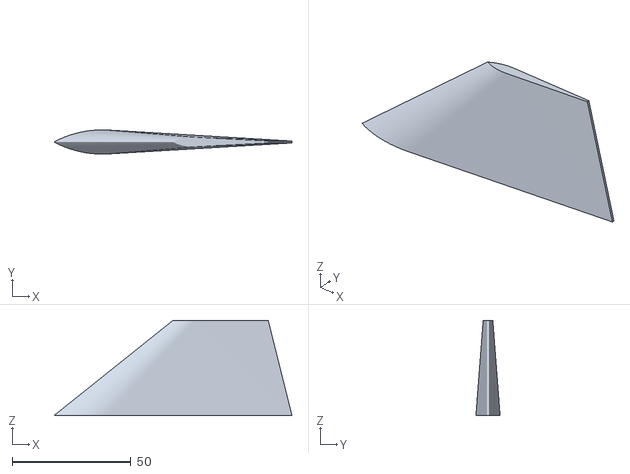
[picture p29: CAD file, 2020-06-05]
parts/fins/new - fin for you.stl
100.0 x 10.2 x 40.0

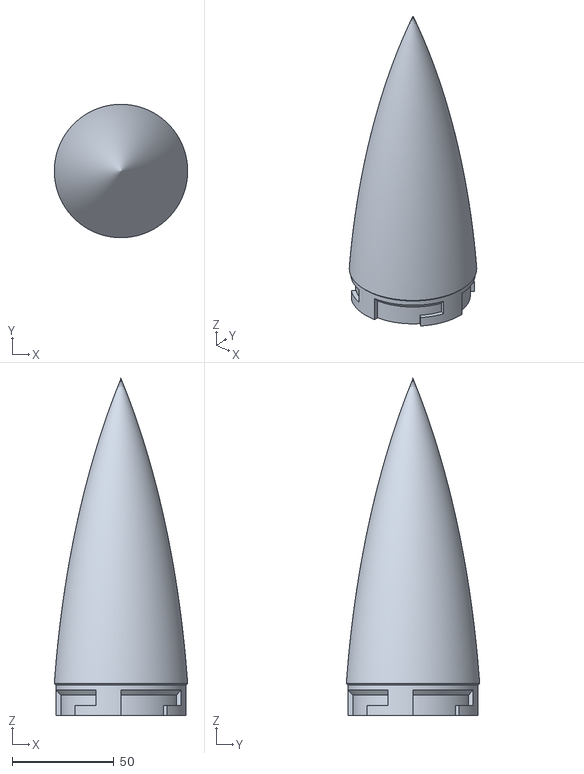
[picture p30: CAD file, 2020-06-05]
parts/Nosecone.stl
65.6 x 65.6 x 165.8

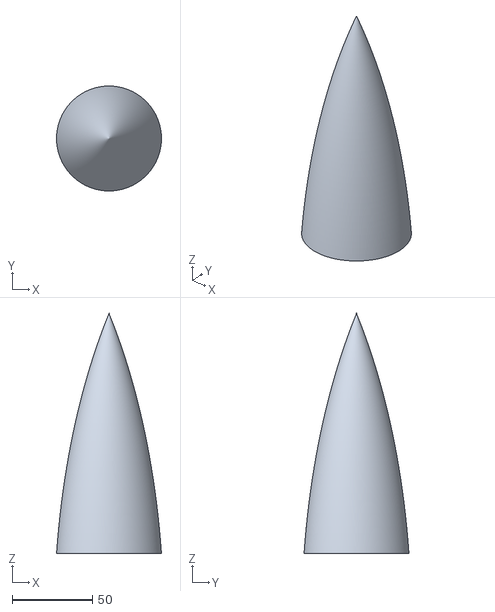
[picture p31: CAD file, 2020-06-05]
parts/fins/new - Nosecone.stl
65.6 x 65.6 x 150.0

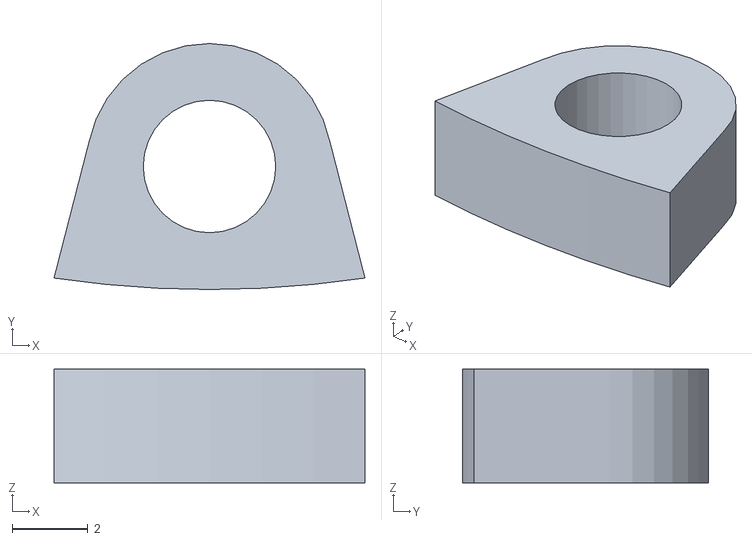
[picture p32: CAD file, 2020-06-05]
parts/Parachute flap holder.stl
8.22 x 6.50 x 3.00

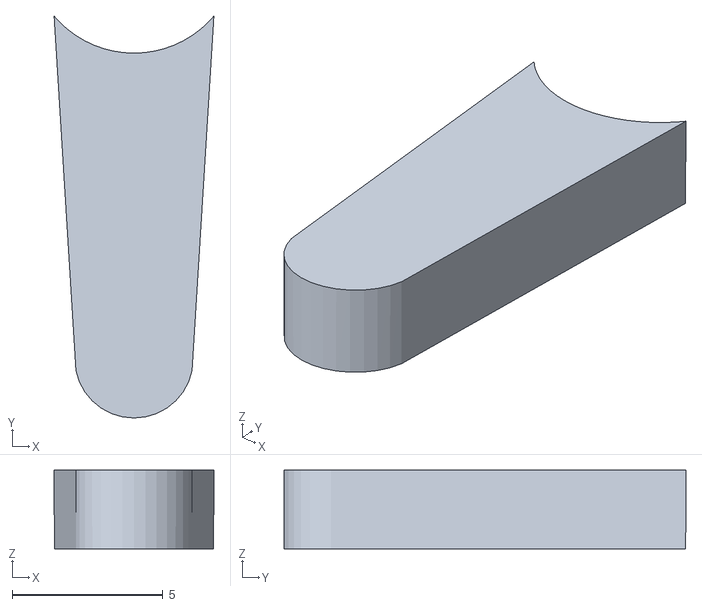
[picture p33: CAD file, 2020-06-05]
parts/Fins.stl
5.30 x 13.3 x 2.61

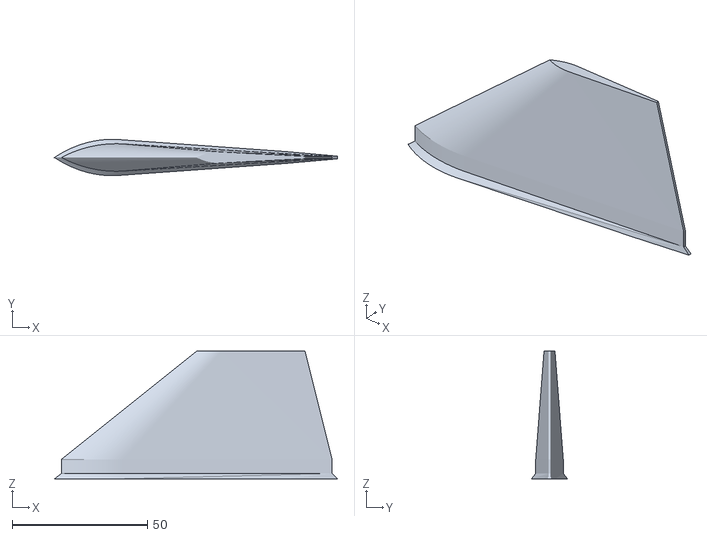
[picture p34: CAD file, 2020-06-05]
parts/fins/fin for you.stl
104.6 x 13.4 x 47.2

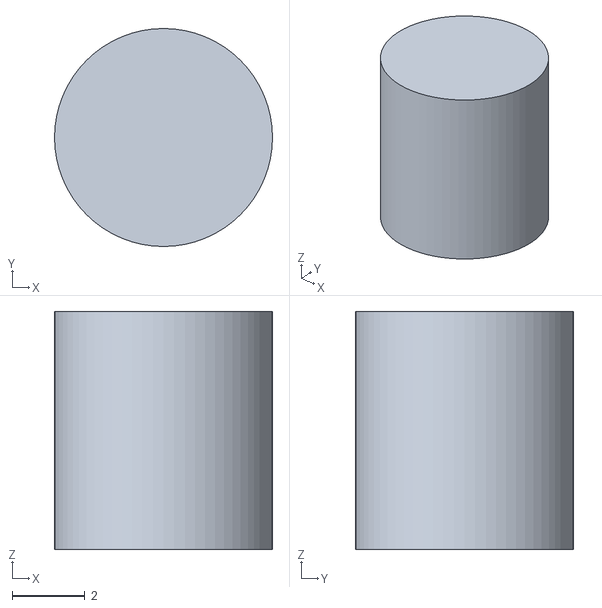
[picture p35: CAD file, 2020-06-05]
parts/Button Guide.stl
6.00 x 6.00 x 6.55

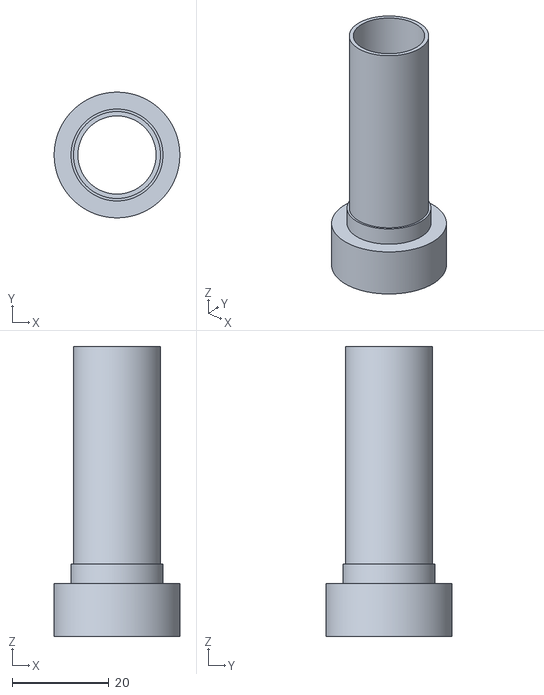
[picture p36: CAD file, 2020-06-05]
parts/Launch Lug Adaptor.stl
26.0 x 26.0 x 60.0

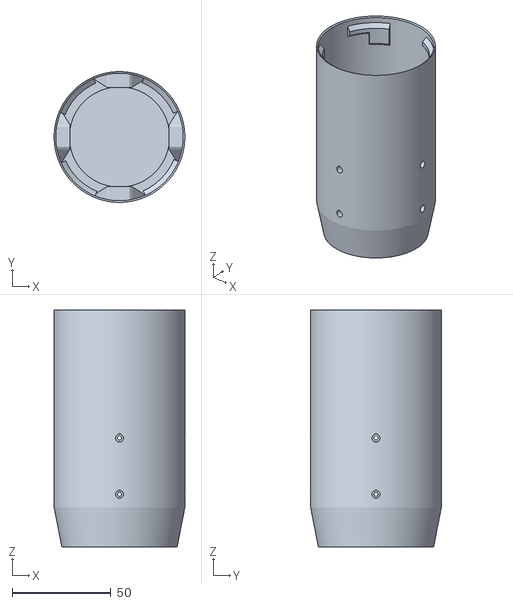
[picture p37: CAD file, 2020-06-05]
parts/Top Body Tube.stl
66.2 x 66.2 x 120.0

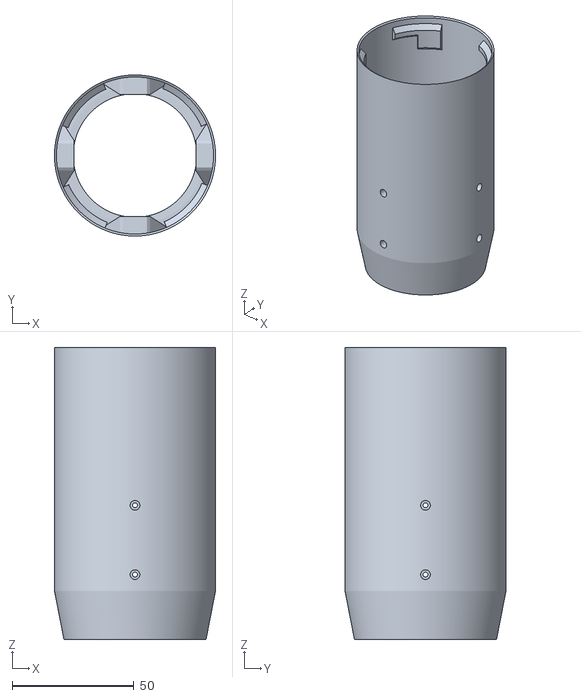
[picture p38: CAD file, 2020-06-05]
parts/Top Body Tube Test.stl
66.2 x 66.2 x 120.0

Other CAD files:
parts/Electronics Bay.stl
parts/Fin Slot.stl
parts/Button Guide.blend
parts/Electronics Bay.blend
parts/Fin Slot.blend
parts/Fins.blend
parts/Launch Lug Adaptor.blend
parts/Nosecone.blend
parts/Parachute flap holder.blend
parts/Servo Stand bottom.blend
parts/Top Body Tube.blend
parts/fins/fin for you.blend
parts/fins/smol fin.blend

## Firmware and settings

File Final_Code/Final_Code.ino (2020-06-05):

#include <Wire.h>
#include <Servo.h>

//SD Card
#include <SPI.h>
#include <SD.h>
#define chipSelect 4

//Gyro
#include <MPU6050.h>
MPU6050 mpu;
#define timeStep 0.01
double pitch = 0,    yaw = 0,    roll = 0;
double PitchOut = 0, YawOut = 0, RollOut = 0, Para = 0;  //

//Altimeter
#include "SparkFunBME280.h"
BME280 Altimeter;
int Altitude;
int Apogee;
#define V1 8.75  //Speed with one parachute
#define V2 4.75  //Speed with all deployed

Servo North;        //to pin 5
Servo East;         //to pin 6
Servo South;        //to pin 9
Servo West;         //to pin 10
Servo Parachute;    //to pin 3

#define RFactor 5
#define PFactor 10
#define YFactor 10

int LaunchTime, Time;
bool Launched = false;
float Accel;

#define ParachutePin 2        //Connect to parachute detector D8
bool Attached = true;

#define MinimumAlt 50

void setup() {
  Serial.begin(9600);
  North.attach(5);
  East.attach(6);
  South.attach(9);
  West.attach(10);
  Parachute.attach(3);

  Parachute.write(170);

  while (!mpu.begin(MPU6050_SCALE_2000DPS, MPU6050_RANGE_16G)) {
    Serial.println("Could not find a valid MPU6050 sensor, check wiring!");
    delay(500);
  }
  mpu.calibrateGyro();
  mpu.setThreshold(1);

  Wire.begin();
  Altimeter.setI2CAddress(0x76);
  if(Altimeter.beginI2C() == false) Serial.println("Sensor B connect failed");
}

void loop() {

  if(Launched == false){
    //READ ACCELERATION
  }  
  
  if(Accel>30 && Launched == false){
    Launched == true;
    Launchtime = millis();
  }

  if(digitalRead(ParachutePin) == HIGH){ Attached = false; }    //Parachute deployment check

  Altitude = 13504.985*(1-pow((Altimeter.readFloatPressure()/101325.), 0.190289));  

    if(Attached == true){
      Vector norm = mpu.readNormalizeGyro();
        pitch = pitch + norm.YAxis * timeStep;
        roll = roll + norm.ZAxis * timeStep;
        yaw = yaw + norm.XAxis * timeStep;
      
      North.write  (90 + pitch*PFactor - yaw*YFactor + roll*RFactor);
      South.write  (90 - pitch*PFactor + yaw*YFactor + roll*RFactor);
    
      West.write   (90 + pitch*PFactor - yaw*YFactor + roll*RFactor);  
      East.write   (90 - pitch*PFactor + yaw*YFactor + roll*RFactor);
    } else {
      North.write(5);East.write(5);South.write(5);West.write(5);

    if(Altitude <= MinimumAlt){Parachute.write(10)}                        //If minimum altitude is reached
    
    if(Time >= (Apogee-((36.5)*V2)*1000/(V1-V2)) ){Parachute.write(10)}    //Calculated time    
    }

  if(Altitude > Apogee){Apogee = Altitude;}  //Apogee
  Time = millis() - Launchtime;              //Time from launch


  if(Launched == true){
    File dataFile = SD.open("datalog.txt", FILE_WRITE);   
    dataFile.print(Time);
    dataFile.print(",");
    dataFile.print(Altimeter.readFloatPressure());  //Raw pressure data
    dataFile.print(",");
    dataFile.print(Altitude);   //Calculated pressure
    dataFile.close();    
  }

  Serial.print(" Pitch = ");
  Serial.print(pitch);
  Serial.print("   Roll = ");
  Serial.print(roll);  
  Serial.print("   Yaw = ");
  Serial.println(yaw);
  
}

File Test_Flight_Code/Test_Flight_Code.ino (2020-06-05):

/*
 *      Setup Diagram (top down):
 * 
 *          Servo 9          Servo 6
 *     
 *         
 *                    Gyro
 *     
 *     
 *          Servo 10         Servo 5
 * 
 * 
 *      Pitch (tilt along this axis:     <------>)
 *      
 *      Yaw   (along this axis:)
 *                    /\
 *                    ||
 *                    ||
 *                    ||
 *                    ||
 *                    ||
 *                    \/
 *      Roll  (⑨)
 *
 */

#include <Wire.h>
#include <Servo.h>

//SD Card
#include <SPI.h>
#include <SD.h>
#define chipSelect 4

//Gyro libary: https://github.com/jarzebski/Arduino-MPU6050
#include <MPU6050.h>
MPU6050 mpu;
#define timeStep 0.01
double pitch = 0,    yaw = 0,    roll = 0,    Para = 0;
float Accel;


//Altimeter libary from sparkfun: https://github.com/sparkfun/SparkFun_BME280_Arduino_Library
#include "SparkFunBME280.h"
BME280 Altimeter;
int Altitude;

//Servos
Servo BRServo;        //to pin 5
Servo TRServo;        //to pin 6
Servo TLServo;        //to pin 9
Servo BLServo;        //to pin 10
Servo Parachute;      //to pin 3

int BRServoAng, TLServoAng, BLServoAng, TRServoAng;

//Konstants for tuning
#define PFactor 1
#define YFactor 1
#define RFactor 1
#define MinAngle 45
#define MaxAngle 135

digittlaRead(pinsense,(;

//Flight variables
#define ParachutePin 2        //Connect to parachute detector D2
int Launchtime = 0;           //Time between turning on and launch
double FlightTime = 0;           //Time since launch
bool Launched = false;        //Is the rocket launched?
bool Attached = true;         //Is the rocket's first parachute still attached (not deployed)?

                          //------------------------//
void setup() {            //------SETUP  BEGIN------//
                          //------------------------//
  //Connect servos
  Serial.begin(115200);
  BRServo.attach(5);
  TRServo.attach(6);
  TLServo.attach(9);
  BLServo.attach(10);
  Parachute.attach(3);

  Parachute.write(170);  //Sets parachute servo to LOCKED position

  //Gyro+Accel start with settings: 250DPS (degrees/second), 16G (maximum 16Gs, expecting 10.7G MAX)
        while (!mpu.begin(MPU6050_SCALE_250DPS, MPU6050_RANGE_16G)) {
          Serial.println("Could not find a valid MPU6050 sensor, check wiring!");
          delay(500);
        }
        mpu.calibrateGyro();
        mpu.setThreshold(1);

  //Start Altimeter
        Wire.begin();
        Altimeter.setI2CAddress(0x76);
        if (Altimeter.beginI2C() == false) Serial.println("Sensor B connect failed");

  BRServo.write(90);  //Set servos straight up
  TLServo.write(90);
  BLServo.write(90);
  TRServo.write(90); 
  //delay(3000); 
                          //------------------------//
}                         //-------SETUP  END-------//
                          //------------------------//
                          
                          //------------------------//
void loop() {             //-------LOOP BEGIN-------//
                          //------------------------//
  //Acceleration
  Vector rawAccel = mpu.readRawAccel();
  Vector normAccel = mpu.readNormalizeAccel();
  Accel = normAccel.ZAxis;  //Variable to Z axis acceleration

  //Angles
  Vector norm = mpu.readNormalizeGyro();
  pitch = pitch + norm.YAxis * timeStep;
  roll = roll + norm.ZAxis * timeStep;
  yaw = yaw + norm.XAxis * timeStep;

  //Altitude
  Altitude = Altimeter.readFloatPressure();
  
    //READOUTS
  Serial.print("Pitch : ");
  Serial.print(pitch);
  Serial.print("   Yaw : ");
  Serial.print(yaw);
  Serial.print("   Roll : ");
  Serial.print(roll);  
  Serial.print("   Acceleration : ");
  Serial.print(Accel);
  Serial.print("   Pressure : ");
  Serial.print(Altitude);
  Serial.print("   Launched : ");
  Serial.print(Launched);
  Serial.print("   Attached : ");
  Serial.print(Attached);
  Serial.print("   Launchtime : ");
  Serial.print(Launchtime);
  Serial.print("   Flighttime : ");
  Serial.println(FlightTime);
  
  

  if (Accel > 15 && Launched == false) {  //Find launch time (once rocket feels 2.5G at about 0.1s)
    Launched = true;                     //Only happens once since bool Launched only false once
    Launchtime = millis();
  }

  if(Launched == true){
    FlightTime = millis() - Launchtime;   //Find time from blast off (ONLY if launched)
  }

  if(digitalRead(ParachutePin) == HIGH) { //Pin normally connected to ground, once parachute deploys, goes floating
    Attached = false;
  }

  if (Attached == true) {     //Fin correction active when parachute not attached
    BRServoAng = 90 + pitch*PFactor + yaw*YFactor + roll*RFactor;
    TLServoAng = 90 - pitch*PFactor - yaw*YFactor + roll*RFactor;
    BLServoAng = 90 - pitch*PFactor + yaw*YFactor + roll*RFactor;
    TRServoAng = 90 + pitch*PFactor - yaw*YFactor + roll*RFactor;   
     
    BRServo.write  (constrain(BRServoAng, MinAngle, MaxAngle));
    TLServo.write  (constrain(TLServoAng, MinAngle, MaxAngle));
    BLServo.write  (constrain(BLServoAng, MinAngle, MaxAngle));
    TRServo.write  (constrain(TRServoAng, MinAngle, MaxAngle));   //90 is straight up  
  } 
  else
  {
    BRServo.write(5); TRServo.write(5); TLServo.write(5); BLServo.write(5); //Try to slow down rocket
  }

  if (FlightTime > 25000){
    Parachute.write(10);      //Move parachute servo after 25 seconds (after launch) to deploy secondary parachutes
    //Serial.print("Secondary Parachute deployed");
  }    


  //Datalogging
  if(FlightTime < 60000){
  File dataFile = SD.open("DATALOG.TXT", FILE_WRITE);
  dataFile.print(FlightTime);                                       //Time,
  dataFile.print(",");          dataFile.print(Altitude);           //Raw pressure data,
  dataFile.print(",");          dataFile.print(normAccel.ZAxis);    //Acceleration,
  dataFile.print(",");          dataFile.print(pitch);              //Pitch,
  dataFile.print(",");          dataFile.print(roll);               //Roll,
  dataFile.print(",");          dataFile.println(yaw);              //Yaw
  dataFile.close();
  }
  
                          //------------------------//
}                         //--------LOOP END--------//
                          //------------------------//
